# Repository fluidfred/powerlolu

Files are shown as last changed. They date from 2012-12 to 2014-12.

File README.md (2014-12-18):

powerlolu
=========

High Power Pololu Board (Powerlolu) based on A4989 - can be connected to RAMPS Pololu port

Description
------------

Powerlolu can drive stepper motors up to 500 Watts, drawing currents up to 10 Amps. 
The existing Pololu boards found in common RepRap 3D printers are at their limits when 
driving the 2 Nema17 z-axis stepper motors in parallel. 

Continuous z-axis movement can cause the board to overheat. These boards hardly drive 
stepper motors bigger than a Nema17. To avoid overheating or to drive larger motors a 
more powerful driver board is needed.

The Powerlolu board enables the use of bigger stepper motors for a wide range of uses. 
This could be the conversion of manual milling machines into computer controlled milling 
machines (CNC-Machines) using the affordable electronics such as Arduino and RAMPS. 
Building 3D printers with a larger print volume or with larger extruders would be possible.

Tested the design by connecting a Nema43 stepper motor by Nanotec Electronic (capable of 
6.6 Amps per coil, Torque 2000Ncm, Weight 8,4kg) to a Powerlolu attached to a 3D printer's 
RAMPS X-port.

A short video of the new driver can be seen on YouTube at
https://www.youtube.com/watch?v=G9FWvhZI7rs .

After two hours of motor usage the Powerlolu board only got luke warm - however see Installation Note

The schematics for the Powerlolu driver are freely available at https://github.com/fluidfred/powerlolu.

Technical specifications:

* 3-wire control with DIR, STEP, Enable-signal, compatible to the Pololu board
* Supply voltage of the stepper motor from 12V to 50V
* Adjustable stepping via SMD-jumper, 1, 1/2, 1/4, 1/16 (default) steps
* Precision pot to adjust the current limiter
* no extra heat sink required due to passive cooling up to NEMA 23 stepper motors.
* Molex snap-on connector for connecting the RAMPS board to the Powerlolu
* Dimensions PCB: 75.5mm x 65mm

Important installation note:
----------------------------
Observe the heat emission when using stepper motors larger than NEMA 23. 
If necessary, implement a cooling system, i.e. heat sinks mounted at the power-Mosfets and a fan. 
Each individual Powerlolu should be protected by connecting an appropriate fuse between VBB (X2) 
and the power source of the stepper motor.

More installation notes can be found under http://wiki.germanreprap.com/en/handbuch/powerlolu concerning wiring with RAMPS and current limiter adjustment.

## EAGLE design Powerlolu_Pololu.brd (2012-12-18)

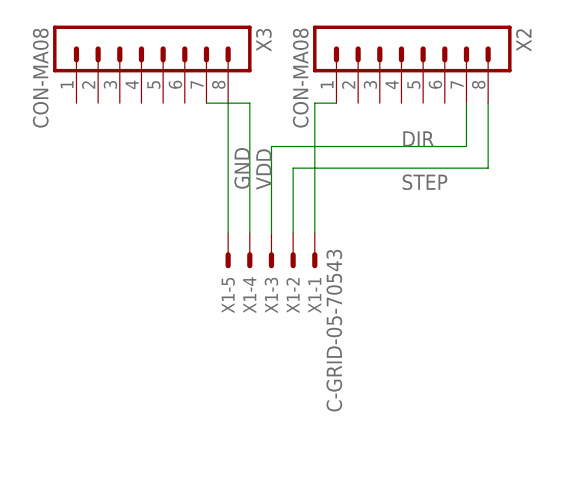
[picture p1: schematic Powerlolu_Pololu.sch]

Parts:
X1: C-GRID-05-70543; 70543-05
X2, X3: CON-MA08; MA08

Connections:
DIR: X1.3, X2.7
GND: X1.5, X3.8
unnamed: X1.1, X2.1
STEP: X1.2, X2.8
VDD: X1.4, X3.7

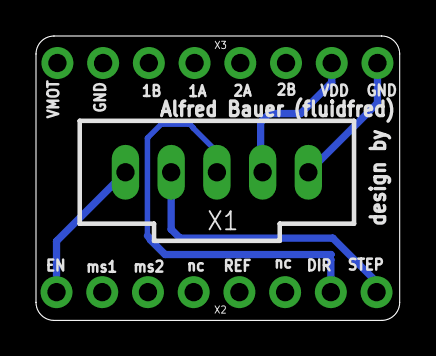
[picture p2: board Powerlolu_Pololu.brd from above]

Board: 2 copper layers, 20.2 x 15.8 mm, 3 parts (0 on the bottom side), 5 nets.

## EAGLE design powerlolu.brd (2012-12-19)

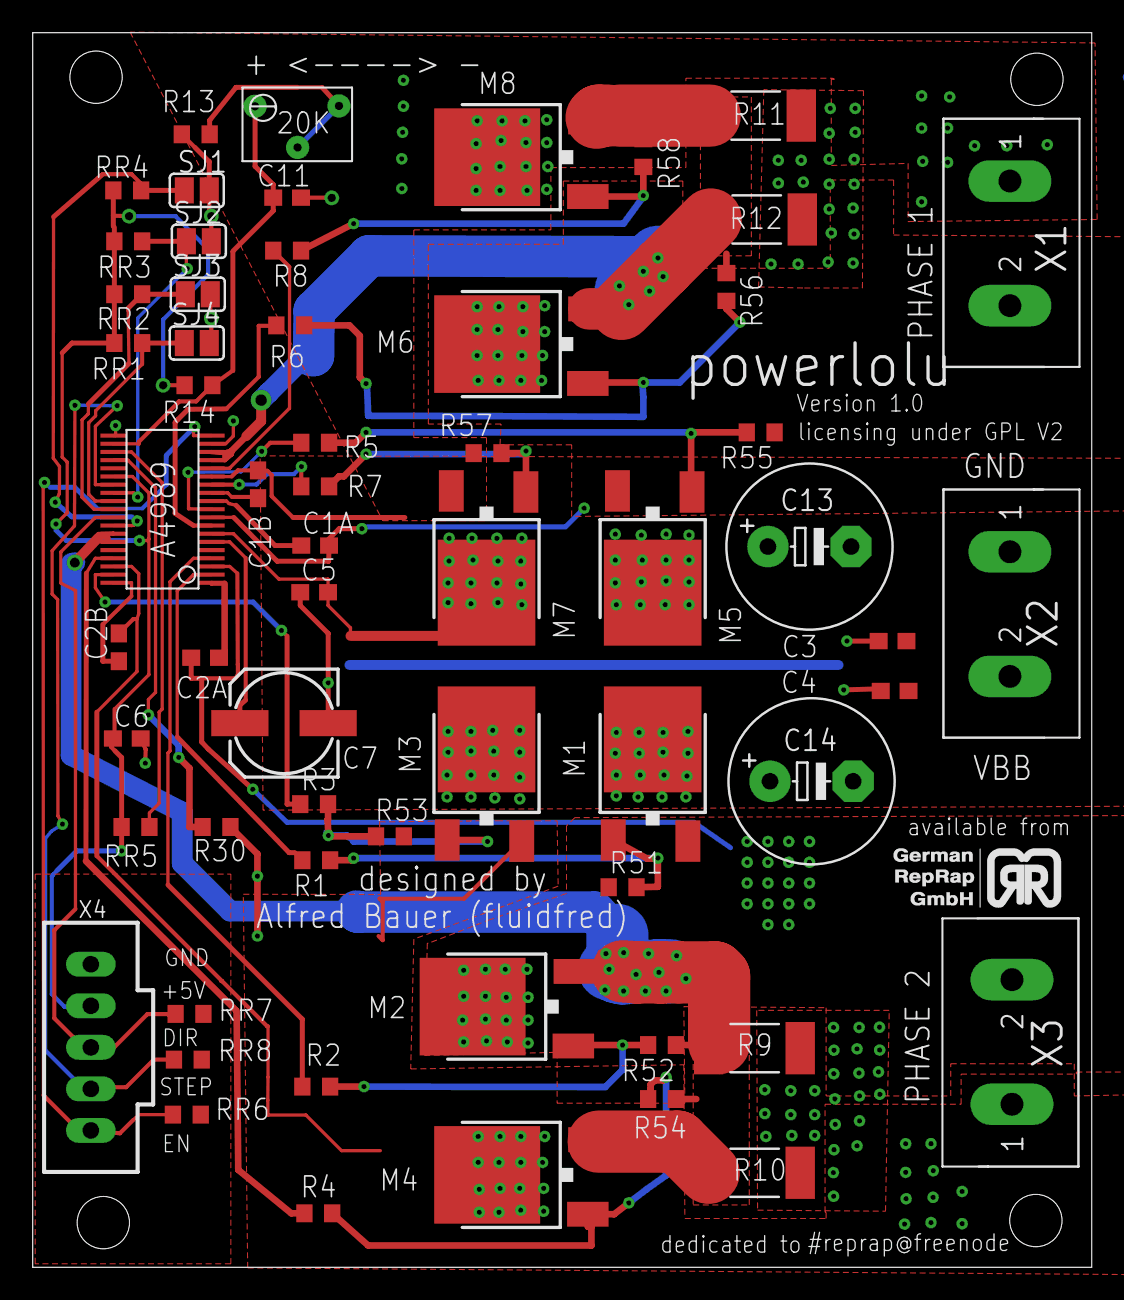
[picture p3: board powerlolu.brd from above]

Board: 2 copper layers, 64.8 x 75.5 mm, 61 parts (0 on the bottom side), 41 nets.

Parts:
A4989: A4989; TSSOP39
C1A, C1B, C2A, C2B, C3, C4, C5, C6, C11: 0.1u; C0603
C7: 10u; 153CLV-0605
C13, C14: 100u; E5-10,5
M1, M2, M3, M4, M5, M6, M7, M8: IRLR024N; TO252
R1, R2, R3, R4, R5, R6, R7, R8: 33; R0603
R9, R10, R11, R12: 0.1; R2512
R13: 10K; R0603
R14: 22k; R0603
R30: 10k; R0603
R51, R53, R54, R55, R56, R57, R58: 470k; R0603
R52: 470K; R0603
RR1, RR5, RR6, RR7, RR8: 10K; R0603
RR2, RR3, RR4: 10k; R0603
SJ1, SJ2, SJ3, SJ4: SJ
U$1: 20K; BOURNS_3266W
X1, X2, X3: GMGDS32; GMKDS32
X4: C-GRID-05-70543; 70543-05

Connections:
GND: A4989.18, A4989.20, C3.1, C4.1, C5.1, C6.2, C7.-, C11.1, C13.-, C14.-, R9.2, R10.2, R11.2, R12.2, R13.2, R30.2, SJ1.2, SJ2.2, SJ3.2, SJ4.2, X2.1, X4.5
unnamed: A4989.27, RR3.1, SJ2.1
unnamed: A4989.29, RR2.1, SJ3.1
unnamed: A4989.28, RR1.1, SJ4.1
unnamed: M2.1, R2.1, R52.2
unnamed: M1.1, R1.1, R51.2
unnamed: M3.1, R3.2, R53.1
unnamed: M4.1, R4.2, R54.1
unnamed: M6.1, R6.1, R56.2
unnamed: M5.1, R5.1, R55.2
unnamed: M7.1, R7.2, R57.1
unnamed: M8.1, R8.2, R58.1
unnamed: A4989.23, R30.1
unnamed: R13.1, U$1.2, U$1.3
unnamed: A4989.22, RR5.1
unnamed: A4989.21, C11.2, R14.1, U$1.1
unnamed: A4989.37, R3.1
unnamed: A4989.2, R1.2
unnamed: A4989.35, R4.1
unnamed: A4989.4, R2.2
unnamed: A4989.26, RR8.1, X4.2
unnamed: A4989.32, A4989.33, M2.2, M4.2, R9.1, R10.1, R52.1, R54.2
unnamed: A4989.19, RR6.1, X4.1
unnamed: A4989.10, R5.2
unnamed: A4989.13, R7.1
unnamed: A4989.15, R8.1
unnamed: A4989.8, R6.2
unnamed: A4989.12, C1B.1
unnamed: A4989.16, A4989.17, M6.2, M8.2, R11.1, R12.1, R56.1, R58.2
unnamed: A4989.31, RR4.1, SJ1.1
unnamed: A4989.11, C1A.1
unnamed: A4989.1, C2A.1
unnamed: A4989.38, C2B.1
unnamed: A4989.30, RR7.1, X4.3
unnamed: A4989.25, C6.1, R14.2, RR1.2, RR2.2, RR3.2, RR4.2, RR5.2, RR6.2, RR7.2, RR8.2, X4.4
unnamed: A4989.6, C7.+
P1+: A4989.9, C1A.2, M5.2, M6.3, R55.1, X1.2
P1-: A4989.14, C1B.2, M7.2, M8.3, R57.2, X1.1
P2+: A4989.3, C2A.2, M1.2, M2.3, R51.1, X3.2
P2-: A4989.36, C2B.2, M3.2, M4.3, R53.2, X3.1
VBB: A4989.7, C3.2, C4.2, C5.2, C13.+, C14.+, M1.3, M3.3, M5.3, M7.3, X2.2

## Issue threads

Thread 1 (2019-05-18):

Question on BOM

esolares, 2019-05-18:
Hi,

I noticed there was no BOM. I used EAGLE to try and deduce the parts needed, but wasn't sure about the resistor ratings since they only list the Ohm value and not the voltage or watt. I'm assuming they are all supposed to be rated at 50V?

Could you please upload a BOM so that it can be easier to recreate this board?

Thank you for your help,

Edwin

TopCodeTejas, 2020-11-18:
It appears that this repo is dead.(?)

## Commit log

2012-12-18 First Version
    [powerlolu.brd, powerlolu.sch]
2012-12-19 cosmetic changes
    [powerlolu.brd]

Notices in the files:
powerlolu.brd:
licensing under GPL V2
